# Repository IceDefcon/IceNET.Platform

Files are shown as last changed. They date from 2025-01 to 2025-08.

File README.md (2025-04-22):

# CPU & FPGA Embedded Computer Platform

	Artificial Inteligence Drone :: Manual Override

# Current Hardware configuration

	Quartus :: 22.1std.1 Build 917 02/14/2023 SC Lite Edition
	Cyclone IV :: EP4CE15F23C8N
	Cortex-A57 :: 4.9.253-tegra Kernel Module
	Cortex-A57 :: Qt5 GUI & System Application for Master Control

# TODO Hardware

	00. Order LTE module for high speed radio troughput :: Video transmission
	01. Order J-Link Cable :: SEGGER
	02. Attach to CPU @ Ozone Debuger
	03. Design Powered PCB for bus control

# TODO FPGA

	00. Reanalyze Reset Network in FPGA
	01. Reset modules :: Done !
	02. Empty FIFO's
	03. Reconfigure Peripherals :: Reset them through registers

# TODO Software

	00. Fix up parametriation of I2C Controller
	01. I2C burst mode
	02. SPI Driver in FPGA with burst mode
	03. CAN driver in FPGA
	04. Checksum in RTL Code to be send in last byte
	05. UART Console (DMA controller buffer)
	06. Upgrade Console for the functions with arguments
	07. Add a Number of Drone Arm Instances in the DroneCtrl unit
	08. Synchronize lengths of feedback interrupts :: I2C, SPI, PWM
	09. Adjust feedback preambles @ SPI transmissions between Kernel<-->FPGA
	10. Remove concatenation of bytes :: Use single Sector 0 for SPI/DMI configuration
	11. New concept of Ram Disk Commander :: Command ---> Sector number + data size + operation + etc...

# NEXT Task :: Network Stack -> R&D

	-----===[Top Required]===-----

	00. Order Jetson Nano 4K Camera (or two Cameras)
	01. Order SD Card -> 128GB for Accelerated Libraries (Additional @ GPU Support)
	02. Develop Network Stack Controllers for Video Transportation (Investigation of Network Stack Layers)
	03. Send 4K Video from Jetson Nano over Wi-Fi to x86_64 Machines (Optionally use LTE/5G Modules)
	04. x86_64 Machines connected to the same Network receive Drone 4K Video
	05. Develop Backtrack x86_64 Network Stack Video Receive Controller (Again, All Network Stack Layers :: Both Kernel/User Space)
	06. Display Drone Video on x86_64 Authenticated Machines

# CURRENT Task :: Gravitational Assist -> Try 10MHz @ SPI (Check the Noise)

	Already Done!!!

	00. Initialize system threads
	01. Send sensors configuration to FPGA
	02. Send Offload Vector from CPU to FIFO (Then wait for ACK from FPGA)
	03. Enable Pulse Controllers to begin acquisition of data from SPI sensors

	Need to be Computed

	04. Double-check if SPI Controller has burst all required data from Sensors
	05. Store data from all sensors in FIFO (Due to overlapping interrupt signals to Kernel)
	06. Reconfigure SPI/DMA on the secondary side (concatenated sensor data)
	07. Initiate SPI/DMA Transfer :: Possible IRQ Vector @ FPGA->CPU Direction
	08. Initiate SPI/DMA Transfer :: Optional Kernel ISR triggered by GPIO
	09. Send Data from Kernel to User space
	10. Display data @ GUI
	11. Develop Transfer Function for the PID Controllers based on acquisition from sensors
	12. Accelerate Transfer Function using 128 CUDA Core GPU
	13. Compute feedback to FPGA for PWM Motor controllers
	14. Extremely Fast Feedback for each arm of the HEX-Drone ???
	15. Are we up and flying???

# Testing Hardware Modules

	HC-12 - Radio Module 433MHz
	RTC DS1307 - Real time clock
	SYN115 - Radio Module 433MHz
	L3G4200D - Gyroscope Module

# Most Recent TODO

	00. Finish Sensor calibration
	01. Network stack architecture
	02. Char device for Master Controller
	03. Ram Disk Block device for Master Controller

# ICE

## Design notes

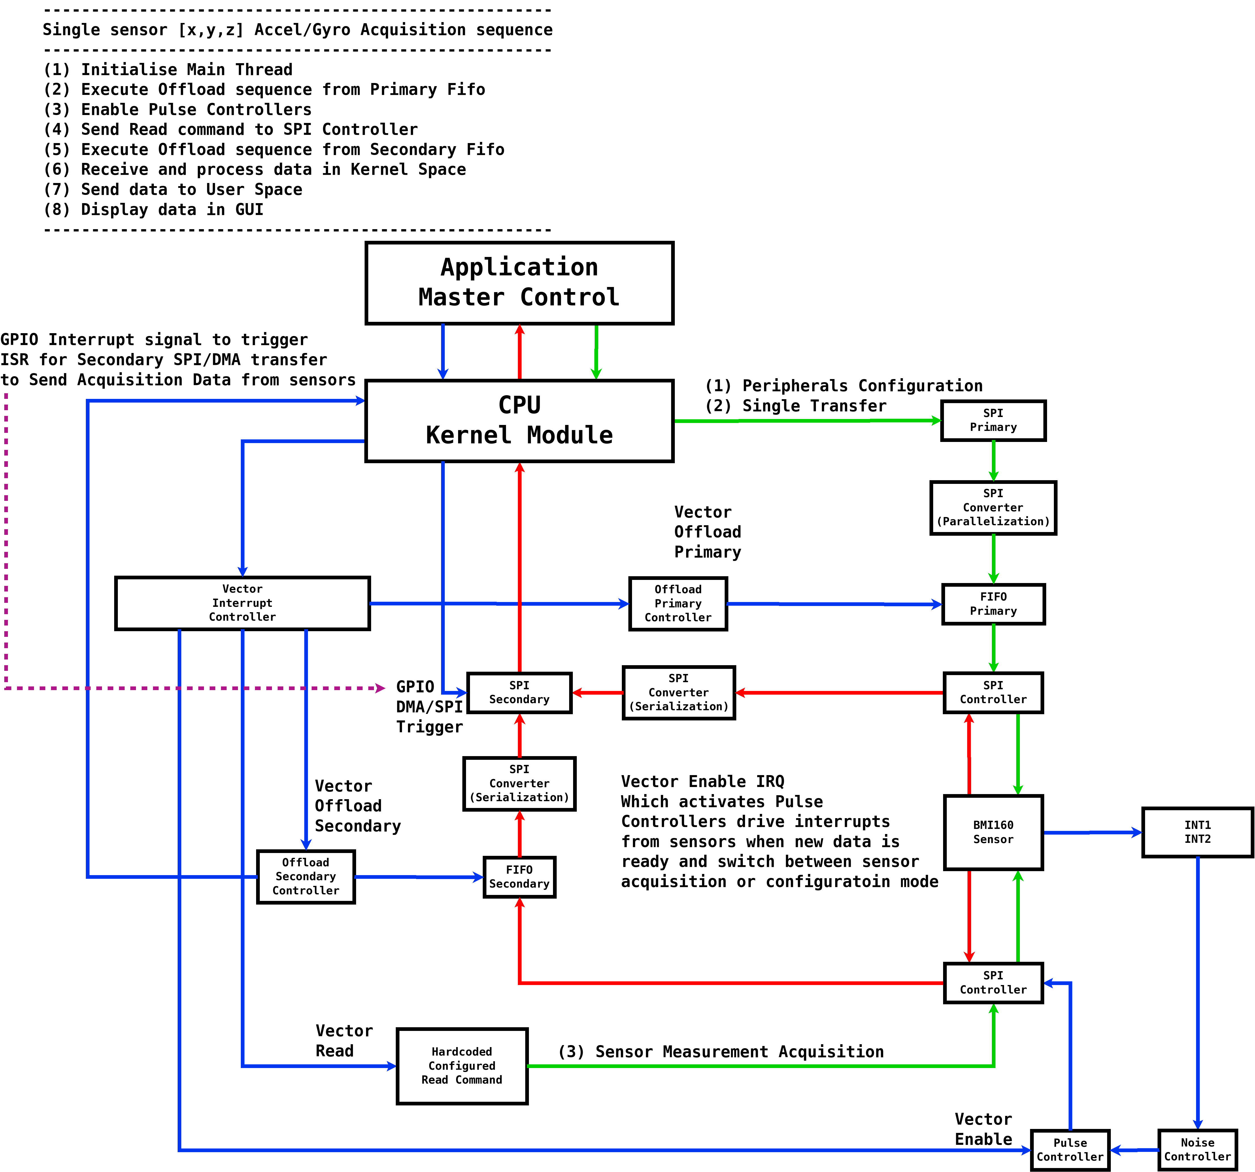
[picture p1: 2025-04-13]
other/architecture/Platform.png

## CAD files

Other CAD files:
debug/tap/DebugUart.stp
rtl/tap/External_SPI_Debug.stp
debug/tap/Debug.stp
rtl/tap/S1_Measurement_Process.stp
rtl/tap/S1_DataProcess.stp
rtl/tap/S1S2_DataProcess.stp
rtl/tap/GeneralTest.stp
rtl/tap/DmaTest.stp
rtl/tap/InterruptGenerator.stp
rtl/tap/SPI_Primary.stp
rtl/tap/SPI_Secondary.stp
rtl/tap/Debug_offload.stp
rtl/tap/reset_Debug.stp
rtl/tap/debugRandom.stp
rtl/tap/SpiController_BMI.stp
rtl/tap/OffloadController.stp
rtl/tap/parallel_spi_debug.stp
rtl/tap/PulseController_Init.stp
rtl/tap/DebounceResetButton.stp
rtl/tap/DebugSpi.stp
rtl/tap/DeviceInterrupts.stp
rtl/tap/InterruptDebug.stp
rtl/tap/InterruptFlow.stp
rtl/tap/SDRAMDriver.stp
rtl/tap/SpiController_RF.stp
rtl/tap/SpiRaw.stp
rtl/tap/bypass_spi.stp
rtl/tap/canDriver.stp
rtl/tap/debug.stp
rtl/tap/fifoCtrl.stp
rtl/tap/i2c.stp
rtl/tap/i2c_SM.stp
rtl/tap/i2c_kernel.stp
rtl/tap/kernel_spi.stp
rtl/tap/primary_spi.stp
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

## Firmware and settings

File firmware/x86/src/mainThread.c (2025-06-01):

#include <linux/kernel.h>
#include <linux/kthread.h>
#include <linux/spinlock.h>
#include <linux/delay.h>
#include <linux/gpio.h>
#include <linux/wait.h>

#include "transmitter.h"
#include "diagnostics.h"
#include "mainThread.h"
#include "x86network.h"
#include "receiver.h"
#include "memory.h"

/////////////////////////
//                     //
//                     //
//                     //
// [STM] State Machine //
//                     //
//                     //
//                     //
/////////////////////////

static DECLARE_WAIT_QUEUE_HEAD(mainThreadWaitQueue);

static mainThreadProcess Process =
{
    .currentState = MAIN_THREAD_IDLE,
    .previousState = MAIN_THREAD_IDLE,
    .stateChanged = false,
    .threadHandle = NULL,
    .irqFlags = 0,
    .threadName = "iceMainThread",
};

/* SET */ void setStateMachine(mainThreadStateType newState)
{
    spin_lock_irqsave(&Process.smSpinlock, Process.irqFlags);
    Process.currentState = newState;
    Process.stateChanged = true; /* Signal that something changed */
    spin_unlock_irqrestore(&Process.smSpinlock, Process.irqFlags);
    wake_up_interruptible(&mainThreadWaitQueue); /* Wake up thread */
}

/* GET */ mainThreadStateType getStateMachine(void)
{
    mainThreadStateType state;
    spin_lock_irqsave(&Process.smSpinlock, Process.irqFlags);
    state = Process.currentState;
    spin_unlock_irqrestore(&Process.smSpinlock, Process.irqFlags);
    return state;
}

static const char* getMainThreadStateString(mainThreadStateType type)
{
    static const char* mainThreadStateStrings[] =
    {
        "MAIN_THREAD_IDLE",
        "MAIN_THREAD_NETWORK_ICMP_PING",
        "MAIN_THREAD_NETWORK_ARP_REQUEST",
        "MAIN_THREAD_NETWORK_NDP_REQUEST",
        "MAIN_THREAD_TCP_TRANSMISSION",
        "MAIN_THREAD_UDP_TRANSMISSION",
        "MAIN_THREAD_DONE"
    };

    if (type >= 0 && type < MAIN_THREAD_AMOUNT)
    {
        return mainThreadStateStrings[type];
    }
    else
    {
        return "UNKNOWN_MAIN_THREAD";
    }
}

static int mainThread(void *data)
{
    mainThreadStateType state;
    showThreadDiagnostics(Process.threadName);

    while (!kthread_should_stop())
    {
        /* Sleep until stateChanged or stop signal */
        wait_event_interruptible(mainThreadWaitQueue, Process.stateChanged || kthread_should_stop());

        if (kthread_should_stop())
        {
            break;
        }

        /* Clear flag after wake */
        spin_lock_irqsave(&Process.smSpinlock, Process.irqFlags);
        Process.stateChanged = false;
        spin_unlock_irqrestore(&Process.smSpinlock, Process.irqFlags);

        state = getStateMachine();

        if (Process.previousState != Process.currentState)
        {
            printk(KERN_INFO "[CTRL][STM] mainThread State Machine %d->%d %s\n", Process.previousState, Process.currentState, getMainThreadStateString(Process.currentState));
            Process.previousState = Process.currentState;
        }

        switch (state)
        {
            case MAIN_THREAD_IDLE:
                /* Nothing to do */
                break;

            case MAIN_THREAD_NETWORK_ICMP_PING:
                printk(KERN_INFO "[CTRL][STM] mode -> MAIN_THREAD_NETWORK_ICMP_PING\n");
                char ip_str[16];
                __be32 ip;

                /**
                 * TODO :: Do we need configurable Network Mask
                 *
                 * Ping current network mask -> IceNET :: 192.168.8.0/24
                 * /24 -> 11111111 11111111 11111111 00000000
                 * First 24-Bits are not modifiable
                 * do we have range 0 to 255
                 * for the last 8-Bits
                 *
                 */
                for (int i = 1; i < 255; i++)
                {
                    snprintf(ip_str, sizeof(ip_str), "192.168.8.%d", i);
                    ip = in_aton(ip_str);
                    icmpSendPing(ip);
                    msleep(50);
                }
                printActiveHosts();
                setStateMachine(MAIN_THREAD_DONE);
                break;

            case MAIN_THREAD_NETWORK_ARP_REQUEST:
                printk(KERN_INFO "[CTRL][STM] mode -> MAIN_THREAD_NETWORK_ARP_REQUEST\n");
                arpSendRequest();
                setStateMachine(MAIN_THREAD_DONE);
                break;

            case MAIN_THREAD_NETWORK_NDP_REQUEST:
                printk(KERN_INFO "[CTRL][STM] mode -> MAIN_THREAD_NETWORK_NDP_REQUEST\n");
                ndpSendRequest();
                setStateMachine(MAIN_THREAD_DONE);
                break;

            case MAIN_THREAD_TCP_TRANSMISSION:
                printk(KERN_INFO "[CTRL][STM] mode -> MAIN_THREAD_TCP_TRANSMISSION\n");
                tcpTransmission();
                setStateMachine(MAIN_THREAD_DONE);
                break;

            case MAIN_THREAD_UDP_TRANSMISSION:
                printk(KERN_INFO "[CTRL][STM] mode -> MAIN_THREAD_UDP_TRANSMISSION\n");
                udpTransmission();
                setStateMachine(MAIN_THREAD_DONE);
                break;

            case MAIN_THREAD_DONE:
                printk(KERN_INFO "[CTRL][STM] mode -> MAIN_THREAD_DONE\n");
                setStateMachine(MAIN_THREAD_IDLE);
                break;

            default:
                printk(KERN_ERR "[CTRL][STM] mode -> Unknown\n");
                return -EINVAL;
        }
    }

    return 0;
}

void mainThreadInit(void)
{
    spin_lock_init(&Process.smSpinlock);
    setStateMachine(MAIN_THREAD_IDLE);

    Process.threadHandle = kthread_create(mainThread, NULL, Process.threadName);

    if (IS_ERR(Process.threadHandle))
    {
        printk(KERN_ERR "[INIT][STM] Failed to create kernel thread. Error code: %ld\n", PTR_ERR(Process.threadHandle));
    }
    else
    {
        printk(KERN_INFO "[INIT][STM] Created kthread for mainThread\n");
        wake_up_process(Process.threadHandle);
    }
}

void mainThreadDestroy(void)
{
    if (Process.threadHandle)
    {
        kthread_stop(Process.threadHandle);
        Process.threadHandle = NULL;
    }
    printk(KERN_INFO "[DESTROY][STM] Destroy State Machine kthread\n");
}

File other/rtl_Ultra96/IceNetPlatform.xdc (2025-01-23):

# Author: Ice.Marek
# IceNET Technology 2025
#

# GPIO
# PIN_E6 :: HD_GPIO_9 :: Pin 16
# PIN_E5 :: HD_GPIO_10 :: Pin 18
#
set_property IOSTANDARD LVCMOS12 [get_ports {gpio_rtl_tri_io[0]}]
set_property PACKAGE_PIN E6 [get_ports {gpio_rtl_tri_io[0]}]

set_property IOSTANDARD LVCMOS12 [get_ports {gpio_rtl_tri_io[1]}]
set_property PACKAGE_PIN E5 [get_ports {gpio_rtl_tri_io[1]}]

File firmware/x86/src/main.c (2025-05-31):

/*!
 *
 * Author: Ice.Marek
 * IceNET Technology 2025
 *
 */
#include <linux/init.h>
#include <linux/module.h>

#include "kernelComms.h"
#include "diagnostics.h"
#include "mainThread.h"
#include "x86network.h"

MODULE_VERSION("1.0");
MODULE_LICENSE("GPL");
MODULE_AUTHOR("Ice.Marek");
MODULE_DESCRIPTION("Master x86 Controler");

//////////////////////////
//                      //
//        [x-86]        //
//        MASTER        //
//         CTRL         //
//                      //
//////////////////////////
static int __init master_controler_init(void)
{
    int ret = 0;

    printk(KERN_INFO "-------------------------------------------------\n");
    printk(KERN_INFO "[BEGIN] Master x86 Controler                     \n");
    printk(KERN_INFO "-------------------------------------------------\n");

    /* Initialise Active Host List */
    initActiveHostList();
    /* Initialise main thread */
    mainThreadInit();
    /* Initialise Broadcas Transmiter */
    networkInit();
    /* Initialise Main Commander */
    mainCommanderInit();

    printk(KERN_INFO "-------------------------------------------------\n");
    printk(KERN_INFO "[READY] Master x86 Controler Loaded Successfuly  \n");
    printk(KERN_INFO "-------------------------------------------------\n");

    return ret;
}

//////////////////////////
//                      //
//        [x-86]        //
//         CTRL         //
//         EXIT         //
//                      //
//////////////////////////
static void __exit master_controler_exit(void)
{
    printk(KERN_INFO "-------------------------------------------------\n");
    printk(KERN_INFO "[TERMINATE] Termination of Master x86 Controler  \n");
    printk(KERN_INFO "-------------------------------------------------\n");

    /* Destroy everything */
    mainCommanderDestroy();
    networkDestroy();
    mainThreadDestroy();
    cleanupActiveHostList();

    printk(KERN_INFO "[TERMINATE] Master Controler Terminated Successfully\n");
}

module_init(master_controler_init);
module_exit(master_controler_exit);

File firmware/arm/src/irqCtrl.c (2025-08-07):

/*!
 * 
 * Author: Ice.Marek
 * IceNET Technology 2025
 * 
 */
#include "irqCtrl.h"
#include "spiWork.h"
#include "watchdog.h"
#include "scheduler.h"

//////////////////////////
//                      //
//                      //
//                      //
//      [ISR] Work      //
//                      //
//                      //
//                      //
//////////////////////////

/* ISR */ static irqreturn_t InterruptFromFPGA_TimerISR(int irq, void *data);
/* ISR */ static irqreturn_t InterruptFromFPGA_WatchdogISR(int irq, void *data);
/* ISR */ static irqreturn_t InterruptFromFPGA_SpiISR(int irq, void *data);

static gpioInputProcessType gpioInputProcess[GPIO_IN_AMOUNT] =
{
    [GPIO_IN_ACTIVATE_SECONDARY_DMA] =
    {
        .irqNumber = 0,
        .gpioName = "SpiGPIO",
        .irqName = "Activate SPI.1",
        .isrFunctionName = "InterruptFromFPGA_SpiISR",
        .flags = IRQF_TRIGGER_RISING,
        .irqFlags = 0,
        .gpioNumber = GPIO_NUMBER_ACTIVATE_SECONDARY_DMA,
        .isrFunction = InterruptFromFPGA_SpiISR,
        .tryLock = 0,
    },

    [GPIO_IN_SCHEDULER_TIMER] =
    {
        .irqNumber = 0,
        .gpioName = "TimerGPIO",
        .irqName = "Scheduler Pulse",
        .isrFunctionName = "InterruptFromFPGA_TimerISR",
        .flags = IRQF_TRIGGER_RISING,
        .irqFlags = 0,
        .gpioNumber = GPIO_NUMBER_SCHEDULER_TIMER,
        .isrFunction = InterruptFromFPGA_TimerISR,
        .tryLock = 0,
    },

    [GPIO_IN_WATCHDOG_TICK] =
    {
        .irqNumber = 0,
        .gpioName = "WatchdogGPIO",
        .irqName = "Watchdog Tick",
        .isrFunctionName = "InterruptFromFPGA_WatchdogISR",
        .flags = IRQF_TRIGGER_RISING,
        .irqFlags = 0,
        .gpioNumber = GPIO_NUMBER_WATCHDOG_TICK,
        .isrFunction = InterruptFromFPGA_WatchdogISR,
        .tryLock = 0,
    },
};

static gpioOutputProcessType gpioOutputProcess[GPIO_OUT_AMOUNT] =
{
    [GPIO_OUT_RESET_FPGA] =
    {
        .gpioName = "FpgaResetGPIO",
        .gpioNumber = GPIO_NUMBER_RESET_FPGA,
    },

    [GPIO_OUT_F1] =
    {
        .gpioName = "DebugF1",
        .gpioNumber = GPIO_NUMBER_F1,
    },

    [GPIO_OUT_F2] =
    {
        .gpioName = "DebugF2",
        .gpioNumber = GPIO_NUMBER_F2,
    }
};

/* ISR */ static irqreturn_t InterruptFromFPGA_TimerISR(int irq, void *data)
{
    if(isShedulerReady())
    {
        setScheduler(SCH_MAIN_20MS);
        queue_work(get_scheduleTimer_wq(), get_scheduleTimer_work());
    }
    else
    {
        queue_work(get_scheduleTimer_wq(), get_scheduleTimer_work());
    }

    return IRQ_HANDLED;
}

/* ISR */ static irqreturn_t InterruptFromFPGA_WatchdogISR(int irq, void *data)
{
    watchdogProcess* tmpProcess = watchdog_getProcess();

    watchdog_spinLockCtrl(CTRL_LOCK);
    if(tmpProcess->indicatorCurrent == 0xFA)
    {
        tmpProcess->indicatorCurrent = 0x00;
    }
    else
    {
        tmpProcess->indicatorCurrent++;
    }
    watchdog_spinLockCtrl(CTRL_UNLOCK);

    return IRQ_HANDLED;
}

/* ISR */ static irqreturn_t InterruptFromFPGA_SpiISR(int irq, void *data)
{
#if 0
    static int counter = 0;

    printk(KERN_INFO "[CTRL][ISR] Interrupt No[%d] received from FPGA @ Pin [%d] :: TODO Checksum comparsion\n", counter, GPIO_NUMBER_ACTIVATE_SECONDARY_DMA);
    counter++;
#endif

    /* LOCK */ spin_lock_irqsave(&gpioInputProcess[GPIO_IN_ACTIVATE_SECONDARY_DMA].isrLock, gpioInputProcess[GPIO_IN_ACTIVATE_SECONDARY_DMA].irqFlags);


    /* CHECK */ if(!gpioInputProcess[GPIO_IN_ACTIVATE_SECONDARY_DMA].tryLock)
    {
        gpioInputProcess[GPIO_IN_ACTIVATE_SECONDARY_DMA].tryLock = 1;

        /* QUEUE :: Execution of masterTransferSecondary */
        queue_work(get_masterTransferSecondary_wq(), get_masterTransferSecondary_work());
    }
    else
    {
        printk(KERN_INFO "[CTRL][TASK] Spinlock is already held, skipping\n");
    }

    /* UNLOCK */ spin_unlock_irqrestore(&gpioInputProcess[GPIO_IN_ACTIVATE_SECONDARY_DMA].isrLock, gpioInputProcess[GPIO_IN_ACTIVATE_SECONDARY_DMA].irqFlags);

    return IRQ_HANDLED;
}

/* CLEAR */ void clearIsrLock(void)
{
    gpioInputProcess[GPIO_IN_ACTIVATE_SECONDARY_DMA].tryLock = 0;
}

static int initializeInterruptFromCPU(outputGpioType outGpio)
{
    int ret;

    ret = gpio_request(gpioOutputProcess[outGpio].gpioNumber, gpioOutputProcess[outGpio].gpioName);
    if (ret < 0)
    {
        printk(KERN_ERR "[INIT][ISR] Failed GPIO Request :: Pin [%d]\n", gpioOutputProcess[outGpio].gpioNumber);
    }
    else
    {
        printk(KERN_ERR "[INIT][ISR] Setup GPIO Pin [%d] Request\n", gpioOutputProcess[outGpio].gpioNumber);
    }

    ret = gpio_direction_output(gpioOutputProcess[outGpio].gpioNumber, 0);
    if (ret < 0)
    {
        printk(KERN_ERR "[INIT][ISR] Failed to set GPIO direction :: Pin [%d]\n", gpioOutputProcess[outGpio].gpioNumber);
        gpio_free(gpioOutputProcess[outGpio].gpioNumber);
    }
    else
    {
        printk(KERN_ERR "[INIT][ISR] Setup GPIO Pin [%d] Output\n", gpioOutputProcess[outGpio].gpioNumber);
    }

    return ret;
}

static void destroyInterruptFromCPU(outputGpioType outGpio)
{
    gpio_free(gpioOutputProcess[outGpio].gpioNumber);
    printk(KERN_INFO "[DESTROY][ISR] Destroy GPIO Pin [%d] From CPU\n", gpioOutputProcess[outGpio].gpioNumber);
}
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

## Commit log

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2024-04-25 Rework on the comms thread
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2024-04-28 Reverse the commit
    [spi.stp]
2024-04-28 Testing received data from C Device
    [spi.stp]
2024-04-28 Flex vector for I2C data transfer between user and kernel spaces
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2024-04-28 Base for the SPI Processor
    [spi.stp]
2024-04-28 Ready for I2c Processing
    [spi.stp]
2024-04-29 testing commands on SPI.0 <-> FPGA
    [i2c.stp, spi.stp]
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2024-05-02 Testing direction of signals User->Kernel->Fpga->I2c
    [i2c.stp]
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2024-05-02 Connect SPI to I2C
    [i2c.stp]
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2024-05-03 Read I2c from user->krenel
    [i2c.stp, spi.stp]
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2024-05-04 Adding preamble to SPI transfers
    [i2c.stp]
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2024-05-04 Setup for char device RxData
    [i2c.stp]
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2024-05-05 Add error checks in char Device
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2024-05-06 Preliminary paametrization of state machine for RW operatios
    [fifo.stp, i2c.stp]
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2024-05-07 One byte FIFO computation
    [fifo.stp, i2c.stp, spi.stp]
2024-05-07 TODO :: Must reduce FIFO interrupt to 20ns
    [fifo.stp, i2c.stp]
2024-05-08 Signal Kernel->Fpga over SPI.0 and FPGA->Kernel over SPI.1
    [fifo.stp, i2c.stp]
2024-05-08 Add preambles on both SPI.0 and SPI.1
    [i2c.stp, secondary_spi.stp]
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2024-05-08 Architecture for primary and secondary SPI
    [i2c_SM.stp, primary_spi.stp, spi.stp]
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2024-05-09 Gererate pulse from kernel to FPGA + process to 20ns
    [primary_fifo.stp]
2024-05-09 gpio example of kernel module for p9.14
    [primary_fifo.stp, read_enable.stp]
2024-05-09 Add read request from FIFO
    [primary_fifo.stp, read_enable.stp]
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2024-05-18 Multiple byte offload ready
    [primary_fifo.stp]
2024-05-19 Testing write into gyroscope
    [primary_fifo.stp]
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2024-05-20 Write to I2c from Kernel
    [i2c_SM.stp]
2024-05-20 Read/Write to I2C device is now Working
    [i2c_SM.stp]
2024-05-20 Testing Write via console
    [i2c_SM.stp]
2024-05-20 Parametrized Read/Write from Kernel >> FPGA >> i2c Device
    [i2c_SM.stp, primary_fifo.stp]
2024-05-20 testing SPI on BMI160
    [primary_spi.stp]
2024-05-21 Custom SPI driver in FPGA
    [bypass_spi.stp, i2c_SM.stp, primary_spi.stp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]
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2024-05-23 3/4 Byte communication to i2c bus in FPGA
    [i2c_SM.stp, primary_fifo.stp]
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2024-06-03 Multi instantiation of the class problem :: Work
    [main.cpp]
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2024-06-15 Fix smart pointers multiple constructor call issue
    [main.cpp]
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2024-06-19 Problem with 1ws read
    [pwm.stp]
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2024-08-18 Fix PWM control from GUI
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2024-09-21 Fix Debounce Controller
    [debounce_controller.stp]
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2024-10-02 Base for the Serial Console @ Baudrate 921600
    [uartDriver.stp]
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2024-10-16 Fix UART console
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2024-11-02 Control bytes received from TCP client to Kernel space
    [fifoCtrl.stp]
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2024-11-19 Working at broken rmmod
    [main.c]
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2024-11-20 Swap vfs_write to kernel_write due to kernel upgrade to 5.10.168-ti-r79
    [main.c]
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2024-11-30 Fix test code for ramDisk
    [ramDisk.c]
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2024-12-20 Problem with clearing sector 0 :: TODO
    [ramDisk.c]
2024-12-20 Problem with infinit DMA Transfer
    [ramDisk.c]
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2024-12-21 Dma Engine :: Problem
2024-12-22 Dma Problem :: Partially solved
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2024-12-22 Fix for 32 bits transfer over DMA to FPGA
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2024-12-31 char Device destruction problem
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2025-01-02 Add logic analuze channels 1-6 :: Check 20ms SPI Interrupt delay
    [debug.stp]
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2025-01-03 Fix up Base for the Offload Controller
    [OffloadController.stp]
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2025-01-07 New Offload Controler :: Wait flag in i2c controller
    [OffloadController.stp, i2c_SM.stp]
2025-01-07 New Offload Controler : 1st Byte glitch
    [OffloadController.stp, i2c_SM.stp]
2025-01-07 New Offload Controler :: Fixed Version 1.0
    [OffloadController.stp]
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2025-01-12 UART Controler :: Add Pause between ASCII Symbols
    [uartDriver.stp]
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2025-01-12 UART Controler :: Add busy Flag for breaks between symbols
    [uartDriver.stp]
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2025-01-15 Ram Controller :: Base Problem
    [SDRAMDriver.stp]
2025-01-16 Ram Controller :: Problem 16.01.25
    [SDRAMDriver.stp]
2025-01-17 Ram Controller :: hook up BSD Licenced Module
    [SDRAMDriver.stp]
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2025-01-17 Add PLL for SDRAM Controller :: Still Problem
    [SDRAMDriver.stp]
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2025-01-18 SDRAM Controller :: Another Problem
    [SDRAMDriver.stp]
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2025-01-20 SDRAM Controller :: Time constraint Problem
    [SDRAMDriver.stp]
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2025-01-21 SDRAM Controller :: Still problem
    [SDRAMDriver.stp]
2025-01-22 SDRAM Controller :: Still not working
    [SDRAMDriver.stp]
2025-01-24 Ram Disk Commander server kill fixed
    [main.cpp]
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2025-02-01 Fix DMA reconfiguration :: New Offload Controler Required
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2025-02-04 Ram Controller :: Still not working
    [SDRAMDriver.stp]
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2025-02-12 Spi Controller :: Done but interrupt not connected
    [InterruptFlow.stp, SpiController.stp, rf905.stp]
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2025-02-13 Spi Controller :: Fixed for nRF905 Module
    [SpiController.stp]
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2025-02-18 RamDisk Refactor :: Fix Dma Engine Sector
2025-02-19 Fix ADXL345 interrupt at data ready + Add interrupt pins to VHDL
    [InterruptFlow.stp, i2c_SM.stp]
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2025-02-21 Add burst size for I2C and Device ID for SPI controllers
    [SpiController_RF.stp]
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2025-02-25 Timing Analysis :: Remove Load and Clear RAM from the Commander
    [SDRAMDriver.stp]
2025-02-25 Timing Analysis :: Ram Controller Works @ Serious Timing Issue
    [SDRAMDriver.stp]
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2025-02-27 SDRAM Controller Issue :: Part 1
    [SDRAMDriver.stp, SpiController_BMI.stp]
2025-02-28 Use 1GHz clock to generate shifted by 180° SDRAM Clock
    [SDRAMDriver.stp]
2025-02-28 Ram Controller (Fix Timing) :: Part 1
    [SDRAMDriver.stp]
2025-02-28 Ram Controller (Fix Timing) :: Part 2
    [SDRAMDriver.stp]
2025-02-28 Ram Controller Timing Fixed :: Remove 1GHz Clock
    [SDRAMDriver.stp]
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2025-03-04 Some timing analysis fixes
    [DebugSpi.stp, SpiRaw.stp]
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2025-03-09 Add I2C protection + replace char with uint8_t
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2025-03-09 Fix RamDisk @ 4.9.253-tegra
    [main.c, ramDisk.c, spiDma.c]
2025-03-10 Fix GPIO numbers for Interrupts
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2025-03-17 Fix-up read byte :: Still 1-bit glitch
    [DebugSpi.stp, SpiController_BMI.stp]
2025-03-17 Fix-up Write on SPI2
    [SpiController_BMI.stp]
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2025-03-18 Fix SPI Write Config :: FPGA Side
    [DebugSpi.stp, SpiController_BMI.stp]
2025-03-18 Fix SPI Write Config :: CPU Side
    [spiDma.c]
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2025-03-21 Base for the Pulse Controller for data transmission to JN
    [DeviceInterrupts.stp, S1_DataProcess.stp, SpiController_BMI.stp]
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2025-03-23 Adding fixed spi
2025-03-24 Fix SPI read + Enable Pulse Controller
    [S1_DataProcess.stp]
2025-03-24 Fix-up delay string print
2025-03-24 Fix SPI Controller
    [S1_DataProcess.stp]
2025-03-25 Pulse Controller ready for main measurement unit :: interrupt controlled
    [PulseController_Init.stp, S1_DataProcess.stp, S1_Measurement_Process.stp]
2025-03-25 Fix Metastability problem in SPI Controler SM + Apply PulseController to Offload Interrupt
    [OffloadController.stp, S1_Measurement_Process.stp]
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2025-03-25 Add Noise Controller to avoid interrupt noisy spikes at bmi160
    [S1_Measurement_Process.stp]
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2025-03-29 Add delay synchronizer (SPI0 and SPI1) + Fix UART
    [S1_Measurement_Process.stp]
2025-03-29 Add Reset from CPU Pinout
    [reset_Debug.stp]
2025-03-30 Connecting Global Reset :: Part 1
    [reset_Debug.stp]
2025-03-30 Connecting Global Reset :: Part 2
    [OffloadController.stp, reset_Debug.stp]
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2025-04-03 Connecting GPU to GUI via UART :: Part 1
    [debugRandom.stp, parallel_spi_debug.stp]
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2025-04-04 Interrupt Vector for the FIFO Offload :: Fpga
    [OffloadController.stp]
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2025-04-05 Fix scheduler + Print Allocation every 300s
2025-04-05 Release GPIO12 and GPIO13 :: Replaced by Interrupt Vector
2025-04-06 [CPU] Testing list in kernel and user space
    [S1_Measurement_Process.stp, debugRandom.stp]
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2025-04-08 [FPGA] Add Data + F1, F2 and F3 Vectors to IRQ Table [Make DataFifo Work]
    [S1_DataProcess.stp, SpiController_BMI.stp, debugRandom.stp]
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2025-04-13 Clear after 500us if no data is collected by Offload Controller
    [Debug_offload.stp, S1_Measurement_Process.stp, debugRandom.stp]
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2025-04-13 [FPGA] Pass data @ 100Hz rate dur to Kernel Lag
    [S1_Measurement_Process.stp]
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2025-04-17 [FPGA] Set output data rate 800Mhz -> 1.25ms
    [Debug_offload.stp, S1_DataProcess.stp, S1_Measurement_Process.stp]
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2025-04-17 Fix reset diodes
    [Debug_offload.stp, reset_Debug.stp]
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2025-05-02 [CPU] Fix missing thead library
    [mainThread.c]
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2025-05-10 [FPGA] Link Speed Vector with FPGA + Delay @ 25k & 400k
    [S1_DataProcess.stp, S1_Measurement_Process.stp, SPI_Secondary.stp]
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2025-05-11 [CPU] Replace Mutex with Spinlock @ 2nd SPI Transfer
    [irqCtrl.c, irqCtrl.h, main.c]
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2025-05-20 [FPGA] Add remain time threshold to Interrupt Generator
    [InterruptGenerator.stp]
2025-05-20 [FPGA] Add remain time threshold to Interrupt Generator :: 1ms Threshold
    [InterruptGenerator.stp]
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2025-05-27 [ARM] Fix-up Debug logs
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2025-05-27 [ARM] Fix-up Drone Control Exit
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2025-05-29 [ARM] Fix up network Hook :: Split at Diagnostic and Communication
2025-05-31 [ARM] Swap priorities for Network communication hooks
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2025-06-10 [ARM] Fix-up Desctructors printouts
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2025-06-10 [FPGA] Setup External Device :: Part 2 (Assume SM Offset for SPI Controller)
    [External_SPI_Debug.stp]
2025-06-10 [FPGA] Setup External Device :: Part 3 (Fix-up SM Offset glitch)
    [External_SPI_Debug.stp]
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2025-06-11 [FPGA] Add External Offload to IRQ Vector logic
    [External_SPI_Debug.stp]
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2025-06-15 [FPGA] [FPGA] Setup External Device :: Part 4 (Re-work offload)
    [External_SPI_Debug.stp]
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2025-06-17 [FPGA] Fix SPI Controller glitch (OFFSET, INIT, BREAK, EXIT)
    [External_SPI_Debug.stp]
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2025-06-30 [FPGA] Everything working after full reset
    [S1S2_DataProcess.stp]
2025-06-30 [CPU] Fix calibration :: Part 1
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2025-07-11 [ARM] Fix-up InitConfig/SkipConfig Action
2025-07-11 [FPGA] Add timed reset after CONF_DONE + Switch Write feedback from REGISTER to DATA + Create UART feedback interface for S1 Demo
    [External_SPI_Debug.stp, S1_Measurement_Process.stp]
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2025-07-25 [ARM] Fix typo
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2025-09-09 Reset sync and delayed UART + Tidy-up
    [Debug.stp, UartDebug.stp]
2025-09-09 Fix up RX-UART
    [UartDebug.stp]
2025-09-09 Make UART Baudrate compatybile with 500K at 50MHz and 2M at 200MHz
    [Debug.stp, UartDebug.stp]
2025-09-10 Down UART clock to 50MHz @ Keep 2M Baud
    [UartDebug.stp]
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2025-09-10 Set RX Baud @ 2M + Optimize and refactor
    [UartDebug.stp, UartVector.stp]
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2025-09-18 Add parametrization of RX Uart + Feedback (including error handle)
    [DebugUart.stp]
